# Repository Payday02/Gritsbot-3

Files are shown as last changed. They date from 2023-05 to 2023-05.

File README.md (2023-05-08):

# Gritsbot-3
This is an upgraded version of Gritsbot 2 from: https://github.gatech.edu/therobotcollective/gritsbot_2

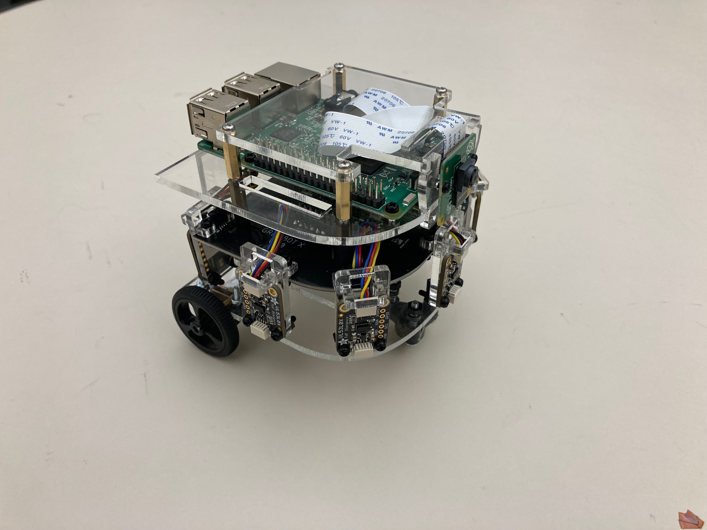
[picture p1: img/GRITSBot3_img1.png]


# Run The Teensy Demo

## 1 - Clone to your repo
```
git clone https://github.com/Payday02/Gritsbot-3.git
```

## 2 - Install Teensyduino / Arduino
For the Teensyduino, follow this link to install on Mac, Linux, and Windows: https://www.pjrc.com/teensy/td_download.html

## 3 - Locate Your Arduino Library
It should be under ```Arduino/Libraries```

## 4 - Copy and Paste the required libraries into the Arduino Library
Go back to the repo where you cloned Gritsbot-3.git
```
cp -a Gritsbot-3/firmware/library/. Arduino/Libraries
```
or

```
cd Gritsbot-3/firmware/library
```
and then copy everything in the library folder, then paste at Arduino/Libraries

## 5 - Run the Expo demo code
Go back to the repo where you cloned Gritsbot-3.git
```
cd Gritsbot-3/firmware/teensyCode/ExpoDemo
```

# Setup Process for the gritsbot\_3 (Need To Fix)(CheckPoint)

# 1 - Making the Base Image

This section details how to make the base image.  Relatively few changes are made to keep the image small.  Once the changes in this section have been made, copy the new image to an SD card and use that as the base image.

## 1 - Load the RPi image onto an SD card

Install latest Raspbian lite to an SD card.  Your .zip file may have a different name. Now, connect the SD card to your computer and unmount it with 
```
umount /dev/<your card>
``` 

You can see the card (probably) with 
```
lsblk
```

```
unzip -p 2018-10-09-raspbian-stretch-lite.zip | sudo dd status=progress of=/dev/sdX bs=4M conv=fsync 
```
 
Navigate to boot partition.  Place ssh, and wpa\_supplicant.conf files in boot partition.

```
cd <path_to>/boot
touch ssh 
touch wpa_supplicant.conf
```

Now, edit the wpa\_supplicant.conf file to something like the following.  Example WPA supplicant file:

```
ctrl_interface=DIR=/var/run/wpa_supplicant GROUP=netdev
update_config=1
country=US

network={
     ssid="Your network name/SSID"
     psk="Your WPA/WPA2 security key"
     key_mgmt=WPA-PSK
}
```

## 2 - Raspi Config

Boot the PI and ssh to it.  Then, launch

```
sudo raspi-config
```

Disable the **SSH console options, splash, and waiting for network on boot.** Enable **boot to the CLI**.  Remain SSHd to the RPi for the next steps.

## 3 - Disable Unused Services 

Add to /boot/config.txt the text

```
# Disable bluetooth
dtoverlay=pi3-disable-bt
```

# 2 - Automated Setup

This section assumes that you have built a base image as previously detailed.

## 1 - Automatic Installation

To install the firmware automatically, move the setup script to the directory /home/pi on the SD card.  Then, place the script setup\_service in the /etc/init.d directory.  When the pi starts, the items in this section will be automatically executed; then, the script deletes itself.  The log for the installation process can be viewed at /var/log/setup\_firmware.log

## 2 - Manual Installation

This section details the installation process for the firmware.  This process can be made automatic via the setup scripts.

### 1 Remove Unused Services

Remove plymouth with 

```
sudo apt-get purge --remove plymouth
```

Disable unused services with 

```
sudo systemctl disable triggerhappy.service
sudo systemctl disable hciuart.service
sudo systemctl disable keyboard-setup.service
sudo systemctl disable dphys-swapfile.service
```

### 2 - Install Docker

This section follows from the official (Docker)[https://docs.docker.com/install/linux/docker-ce/ubuntu/].  First, remove old versions of Docker.

```
sudo apt-get remove docker docker-engine docker.io
```

Next, install Docker using the convenience script.

```
curl -fsSL get.docker.com -o get-docker.sh && export VERSION=18.06 && sh get-docker.sh
```

Now tie Docker to the pi user so that we don't need sudo to use Docker.

```
sudo usermod -aG docker pi
```

### 3 - Clone Git Repos and install Deps

Install pip for python3

```
sudo apt-get install python3-pip
```

To clone the firmware, run
```
sudo apt-get install git
git clone https://github.com/robotarium/gritsbot_2
```

Also, install the MAC discovery repository
```
git clone https://github.com/robotarium/mac_discovery
```

as well as the python serial library used to communicate to the robot.

```
python3 -m pip install pyserial
```

### 4 - WiFi Power Management

Turn off power management by adding the line
```
/sbin/iw dev wlan0 set power_save off
```

in the file /etc/rc.local.  This line disables WiFi power management on boot.

### 5 - Start necessary containers

From wherever the git repository is cloned, run 
```
cd <path_to_gritsbot_2_repo>/docker
./docker_run.sh
./docker_watch.sh
```
which will permanently start a Docker container running the firmware and the watchtower container.  Watchtower watches containers and automatically updates them from Dockerhub.  This watchtower instance
checks and updates **all running containers**, so this instance will also update the MAC container as well.

Start MAC discovery as well with
```
cd <path_to_mac_discovery_repo>/docker
./docker_run.sh
```

# DEPRECATED - Setup Auto Deployment

Most of this info is from the (docker guide to registries)[https://docs.docker.com/registry/deploying/].

Alternatively, you may set up automatic deployment so that each robot updates on its own.  In this case, navigate to the registry directory and 
start the registry for the container.  

Obtain the registry on the **HOST** computer by running 
```
docker run -d -p 5000:5000 --restart=always --name registry registry:2
```
which will pull and run the container.  To only pull,
```
docker pull registry:2
```
should work

Under whatever the registry's computer's IP is, allow this in the file located at 
```
/etc/docker/daemon.json
```
In particular, add the lines
```
{ "insecure-registries": ["<ip_of_registry_computer>:5000"] }
```
Put in the IP right away.  **Errors in this script will kill the Docker service, so be careful!**

For example,
```
{ "insecure-registries": ["192.168.1.8:5000"] }
```
These lines must be added on the **host machine** as well as **all the robots.**  After you've added these lines, restart the Docker service with 
```
sudo /etc/init.d/docker restart
```

Push the firmware to the registry with 
```
docker tag robotarium:firmware <ip_of_registry_computer>:5000/firmware
docker push 192.168.1.8:5000/firmware
```
which will push the firmware container to the registry under the name firmware and the (default) latest tag.

You can check the current images maintained by the registry by checking the catalog with the command
```
curl -X GET 192.168.1.8:5000/v2/_catalog
```

Now, on the robot, navigate to the docker/deploy directory and build the robotarium:updater container.  This container will automatically update 
and restart the firmware container by pulling from the designated registry.

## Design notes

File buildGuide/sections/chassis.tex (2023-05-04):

\section{Chassis Assembly}
\label{sec:chassis}

Now that the main PCB of the GRITSBot X is assembled, it needs a chassis to be placed in. This section will detail how to manufacture and assemble the main chassis of the GRITSBOT X. The files associated with the production are available and editable. The Github repository contains Solid Works part files (SLDPRT), Adobe Illustrator files (AI), and PDF files. The PDF files should be able to be used for direct laser cutting of the chassis. The AI files may be used to edit the position of the cuts and duplicate the cuts for more to be produced at once. The SLDPRT files are what may be edited to change the chassis. Feel free to make whatever changes you would like to the design of the robot. This guide will assume that the construction is being done on the files provided.

\subsection{Laser Cutting the Chassis}
\label{sec:laserCut}

The chassis of the GRITSBot X are cut from $1/8$ inch thick and $1/16$ inch thick acrylic. The final cut pieces can be seen in \cref{fig:acrylicChassisCuts}. The files, \texttt{$GRITSBotX\_1\_8.ai$} and \texttt{$GRITSBotX\_1\_16.ai$} are files ready to produce the chassis through a 3D printer. The \texttt{$GRITSBotX\_1\_8$} is meant to create the $1/8$ inch thick acrylic parts and the \texttt{$GRITSBotX\_1\_16$} is meant to create the $1/16$ inch thick acrylic parts. {\color{red}Note}, these are sized for a $36 \times 24$ inch printer and in some cases the document side must be changed. Other alterations may have to be made for the specific laser cutter you are working on to cut and etch the right places in the file.

 %Laser Cut Pieces Picture
\begin{figure}[h!]
\centering
\subfloat[\label{fig:acrylic8}  $1/8$ inch thick acrylic chassis parts.]{}
\hfill
\subfloat[\label{fig:acrylic16} $1/16$ inch thick acrylic chassis parts.]{}\\
\caption{The $1/8$ (a) and $1/16$ (b) inch thick, custom cut acrylic chassis parts for the GRITSBot X.}
\label{fig:acrylicChassisCuts}
\end{figure}
%End Laser Cut Pieces Picture

Now that the acrylic chassis is cut for the GRITSBot X, the final assembly can begin!

\subsection{Assembling the Base}
\label{sec:base}

\subsubsection{Assembly Steps}
\begin{enumerate}
\item Gather the required materials(\cref{sec:baseMaterials}).
\item Assemble the motors and wheels (\cref{sec:motorAssembly}).
\item Put together the Tamiya caster wheel (\cref{sec:casterAssembly}).
\item Attach the motors and caster to the base plate(\cref{sec:baseAssembly}).
\end{enumerate}

\subsubsection{Required Materials}
\label{sec:baseMaterials}

As with the other sections, the first step is to gather the required materials. These are pictured in \cref{fig:baseMaterials} and listed in \cref{tab:baseMaterials}.

  %Begin Base Part Table
 \begin{table}[h!]
 \centering
\begin{tabular}{lc}
\rowcolor[HTML]{C0C0C0} 
\textbf{Part}  & \textbf{Number Required} 		\\
Acrylic Base Plate			&  1	\\
\rowcolor[HTML]{C0C0C0} 
Wheel               				& 2	\\
Micro-Metal Gear Motor	& 2	\\
\rowcolor[HTML]{C0C0C0} 
Motor Bracket Assembly	& 2   \\
Tamiya Caster Assembly	& 1	\\
\rowcolor[HTML]{C0C0C0} 
Compression Spring		& 3   \\
M3-20 Screw				& 3	\\
\rowcolor[HTML]{C0C0C0} 
M3 Locknut				& 3  
\end{tabular}
\caption{The parts required to assemble the base of the GRITSBot X. \label{tab:baseMaterials}}
\end{table}
 %End Base Part Table
 
 %Base Materials Picture
\begin{figure}[h!]
\centering

\caption{The materials needed to construct the base of the GRITSBot X.}
\label{fig:baseMaterials}
\end{figure}
%End Base Materials Picture

The acrylic base plate should have been laser cut in the previous step. The base plate can be recognized by the three screw holes in a triangular formation in the middle of the curved side of the chassis. This serves as the foundation of the GRITSBot X. The two wheels should come in one package from Pololu with the rubber tires separate from the plastic rims. The micro-metal gear motors from DFRobot come individually with corresponding jumper wires (not pictured here). Do not discard those, they will be used later.  The motor bracket assembly from Pololu should come as a pair with the nuts and screws pictured.  If the screws and nuts are lost they can easily be replaced, they are $\#2-56x7/16''$ screws with $\#2-56$ nuts. The Tamiya caster assembly come in packs of two. You only need one of the two and can keep the other for spare parts or keep this in mind when mass producing. The compression springs are meant as a pseudo suspension on the front caster to alleviate rattling and noise while the M3-20 screw and locknut keep the caster firmly attached to the base.

\subsubsection{Motor and Wheel Assembly}
\label{sec:motorAssembly}

The motor and wheel assembly is fairly straight forward but for consistency between robots details and tips are provided in this section. First, place the tires around the plastic rims. The tires are pretty elastic and can be stretched rather far. The tires on the rims should look like \cref{fig:tires} when finished.

%Tires Picture
\begin{figure}[h!]
\centering

\caption{GRITSBot X wheels fully assembled.}
\label{fig:tires}
\end{figure}
%End Tires Picture

These assembled wheels attach to the motors through a D-shaft. It is important to note the wheels have a flat side and side that sticks out. When pressing the wheel onto the D-shaft of the motor, make sure the flat side of the wheel is facing away from the motor. An easy way to attach the wheel to the D-shaft is to press the motor onto a flat surface through the wheel as pictured in \cref{fig:motorAssembly}. If you assemble this way, {\color{red}{be careful}} the encoder PCB is fragile and the magnetic disc can easily be moved. You are most likely to bend or break off the hall effect sensors (black rectangles sticking out of the PCB), so be careful where you place your hands/fingers when doing this.

%Motor Assembly Picture
\begin{figure}[h!]
\centering
\subfloat[\label{fig:pressMotor}  Pressing the motor D-shaft into the wheel.]{}
\hfill
\subfloat[\label{fig:motorSide} Side view of the motor and wheel assembly.]{}\\
\caption{The motor and wheel assembly pressure fit together.}
\label{fig:motorAssembly}
\end{figure}
%End Motor Assembly Picture

\subsubsection{Tamiya Caster Ball Assembly}
\label{sec:casterAssembly}

Since we are dealing with an \emph{differential drive} platform we need an additional, holonomic point of contact to passively stabilize the system. The GRITSBot X uses a Tamiya caster ball assembly with springs that provide a pseudo-suspension for this point of contact. Assembly instructions come with the Tamiya pack but an altered set of instructions will be provided here.

%Caster Parts Picture
\begin{figure}[h!]
\centering

\caption{The parts required to construct the caster ball assembly.}
\label{fig:casterParts}
\end{figure}
%End Caster Parts Picture

First, only the parts pictured in \cref{fig:casterParts} are needed. The springs, M3-20 screws, and M3 lock-nuts pictured at the bottom of the figure are not included in the kit. \cref{fig:casterAssembly} shows a picture representation of the assembly steps. A written explanation follows.

%Caster Assembly Picture
\begin{figure}[h!]
\centering
\subfloat[\label{fig:caster1} The caster holder with metal ball and cylindrical bearings inside.]{}
\hfill
\subfloat[\label{fig:caster2} Caster ball assembly with top plate properly inserted.]{}\\
\subfloat[\label{fig:caster3} Caster assembly with screws, springs, and plastic rings inserted.]{}
\hfill
\subfloat[\label{fig:casterFinished} The finished caster assembly attached to the bottom acrylic plate of the GRITSBot X.]{}\\
\caption{Process to put together the caster assembly.}
\label{fig:casterAssembly}
\end{figure}
%End Caster Assembly Picture

First, place the metal ball into the plastic caster shell. Place the three metal cylinders on top of the caster ball such that they fall into the rectangular slots in the plastic as seen in \cref{fig:caster1}. Cover this assembly with the second plastic piece provided by the caster kit. The cover should be placed so the triangle of the cover fits in the cutout of the caster ball holder as seen in \cref{fig:caster2}. There should be no gap between the cover and the caster container. Now that the caster is together, place the three M3 screws through the assembly such that the head of the screw is on the caster ball holder side of the assembly. Place the three springs around the screws. Put the three plastic rings over the springs. The screws with spring and plastic ring assembly should look like \cref{fig:caster3}. Push the screws through the holes of the acrylic base and lock them in place by threading them through the lock nuts. Make sure the screw is deep enough into the lock nut that the assembly will not come apart but not so tight that the spring is extremely compressed. This will be adjusted once the wheels are on to level the base.

If done correctly, the assembly should look like \cref{fig:casterFinished}. Test to make sure the caster is free moving by running your hand along the ball. It should move freely. If it doesn't, it's possible one of the metal cylinders came loose during assembly and is restricting the motion. If this is the case, the caster must be reassembled.

\subsubsection{Attaching the Motors and Caster to the Base Plate}
\label{sec:baseAssembly}

Finally, attach the motors to the base of the chassis. This is done by placing the motor bracket over the exposed gear box of the micro-metal gear motor as seen in \cref{fig:bracketMotor}. Note the plastic motor bracket has a rounded and rectangular surface as seen in \cref{fig:bracketDifference}. 

%Motor Bracket Picture
\begin{figure}[h!]
\centering
\subfloat[\label{fig:bracketDifference}  The rectangular opening (left) and curved opening (right) of the motor mounting brackets.]{}
\hfill
\subfloat[\label{fig:bracketMotor} Brackets properly attached to the micro metal gear motors.]{}\\
\caption{Attaching the brackets to the micro-metal gear motors properly.}
\label{fig:properMotorBracket}
\end{figure}
%End Motor Bracket Picture

Make sure the rounded surface rests on the hull of the motor and the rectangular surface rests on the gear box. This motor bracket should be put onto the motor such that the open side is on the same side as the motor connections for the encoder. Place the nut into the hexogonal space on the bracket and thread the screw through the acrylic into the motor bracket. Tighten the caster nuts as appropriate to make the chassis base as level as possible. The final assembly should look like \cref{fig:finalBase}.

%Finished Base Picture
\begin{figure}[h!]
\centering

\caption{The chassis base of the GRITSBot X.}
\label{fig:finalBase}
\end{figure}
%End Finished Base Picture

\subsection{Putting Together the Battery Bracket}
\label{sec:BB}

\subsubsection{Assembly Steps}
\label{sec:BBSteps}

\begin{enumerate}
\item Gather the required materials (\cref{sec:BBParts}).
\item Snap together the acrylic battery box (\cref{sec:BBBox}).
\item Attach the spacers for mounting the battery box and PCB (\cref{sec:BBSpacers}).
\end{enumerate}

\subsubsection{Required Materials}
\label{sec:BBParts}

The battery box assembly is fairly straight forward. The battery box housing is a pressure fit box created by the four $1/16$ inch acrylic parts cut earlier and pictured in the top of \cref{fig:acrylic16}. The housing is then supported and attached to the robot by threaded hexagonal spacers. The full list of materials needed is shown in \cref{tab:BBParts}.

%Begin Battery Box Part Table
 \begin{table}[h!]
 \centering
\begin{tabular}{p{3in}c}
\rowcolor[HTML]{C0C0C0} 
\textbf{Part}  & \textbf{Number Required} 		\\
Acrylic Battery Bracket Top/Bottom		& 2	\\
\rowcolor[HTML]{C0C0C0} 
Acrylic Battery Bracket Side				& 2	\\
4-40, $5/16$ inch Female to Female Hexagonal Standoff	& 4	\\
\rowcolor[HTML]{C0C0C0} 
4-40, $5/16$ inch Male to Female Hexagonal Standoff	& 4  \\
4-40, $3/16$ inch Nylon Male to Female Hexagonal Standoff	& 4
\end{tabular}
\caption{The parts required to assemble the battery bracket of the GRITSBot X. \label{tab:BBParts}}
\end{table}
 %End Battery Box Part Table

\subsubsection{Snapping Together the Battery Box}
\label{sec:BBBox}

The battery box is assembled through pressure/press fitting tabs together to form a box. It should be noted this is a fairly delicate ($1/16$ inch acrylic is brittle and fragile) and precise process. If your laser cutter cuts wider or narrower paths than the one at Georgia Tech, the tab widths may have to be altered.

To begin, press fit two of the side pieces into a top/bottom piece as seen in \cref{fig:box1}. Note, if this seems to tight to do or the tabs don't hold together, the tab widths needs to be adjusted for your laser cutter. The best process to do this is to press in the center tab followed by the outside tabs. Try not to snap the acrylic during this.

%Battery Bracket Assembly Picture
\begin{figure}[h!]
\centering
\subfloat[\label{fig:box1} Battery bracket sides pressure fit into a top/bottom.]{}
\hfill
\subfloat[\label{fig:box2} Final battery bracket assembly.]{}\\
\caption{Pressure/Press fitting together the battery bracket for the GRTISBot X.}
\label{fig:batteryBox}
\end{figure}
%End Battery Bracket Assembly Picture

Finally, press fit the top piece into the assembly just snapped together as seen in \cref{fig:box2}. It is much easier to press fit one side at a time. The joints should rotate fairly easily so you can press one at a time. pressing the assembly into the side of a table or book spine helps tremendously.

\subsubsection{Attaching the Mounting Spacers}
\label{sec:BBSpacers}

Finally, attach the hexagonal spacers to the battery box so it may be mounted to the base of the GRITSBot X and support the PCB in the next steps. Place the four $5/16$ female to female hexagonal spacers between the battery bracket (this can be done one at a time. Screw the four $5/16$ male to female hexagonal spacers into one side of the female to female spacers between the battery bracket. On the other side screw the four $3/16$ male to female nylon hexagonal spacers into the battery bracket. The resulting assembly should look like \cref{fig:finalBatteryBracket}.

 %Battery Bracket Finished Picture
\begin{figure}[h!]
\centering

\caption{The finished battery bracket assembly with hexagonal stand off supports attached.}
\label{fig:finalBatteryBracket}
\end{figure}
%End Battery Bracket Finished Picture

\subsection{Attaching the Cassis Base, Battery Bracket, and PCB}
\label{sec:finishBase}

\subsubsection{Assembly Steps}
\label{sec:finishBaseSteps}

\begin{enumerate}
\item Gather the required materials (\cref{sec:finishBaseMaterials}).
\item Attach the battery box to the chassis base (\cref{sec:BBtoCB}).
\item Attach the PCB to the chassis base assembly (\cref{sec:attachPCB}).
\end{enumerate}

\subsubsection{Required Materials}
\label{sec:finishBaseMaterials}

Connecting the chassis base, battery bracket, and PCB is, again, straightforward and just requires screwing the parts created previously together. The full list of materials needed are in \cref{tab:finishBaseParts}.

%Begin Chassis Base Part Table
 \begin{table}[h!]
 \centering
\begin{tabular}{p{3in}c}
\rowcolor[HTML]{C0C0C0} 
\textbf{Part}  & \textbf{Number Required} 		\\
Assembled Chassis Base from \cref{sec:base}		& 1	\\
\rowcolor[HTML]{C0C0C0} 
Assembled Battery Bracket from \cref{sec:BB}				& 1	\\
Finished PCB from \cref{sec:pcb}	& 1	\\
\rowcolor[HTML]{C0C0C0} 
4-40, $1/4$ inch Screw	& 4  \\
4-40, $3/4$ inch Nylon Male to Female Hexagonal Standoff	& 4\\
\rowcolor[HTML]{C0C0C0} 
3.7V 2500mAh Adafruit Li-Po Battery	& 1
\end{tabular}
\caption{The parts required to combine the chassis base, battery bracket, and PCB of the GRITSBot X. \label{tab:finishBaseParts}}
\end{table}
 %End Chassis Base Part Table

\subsubsection{Attaching the Battery Box to the Chassis Base}
\label{sec:BBtoCB}

The battery bracket assembly (\cref{fig:finalBatteryBracket}, assembly instructions in \cref{sec:BB}) attaches directly to the chassis base (\cref{fig:finalBase}, assembly instructions in \cref{sec:base}) Screw the four 4-40, $1/4$ inch screws,  through the bottom of the four remaining holes in the acrylic base plate into the four 4-40, $5/16$ inch hexagonal standoffs. If done properly, the battery bracket, chassis base assembly should look like \cref{fig:BBtoBC}.

 %Battery Bracket Chassis Finished Picture
\begin{figure}[h!]
\centering

\caption{The base chassis with batter bracket attached.}
\label{fig:BBtoBC}
\end{figure}
%End Battery Bracket Chassis Finished Picture

\subsubsection{Attaching the PCB}
\label{sec:attachPCB}

Attaching the PCB is a little trickier simply because the motor leads danging from the PCB must be attached to the motor and the battery lead must be run in a somewhat smart way. The PCB aligns with the chassis shape, the round part of the board should line up with the round part of the chassis when attached. The top of the PCB has the Teensy micro-controller on it. After orienting it correctly, the four holes on the board should line up with the four 4-40, $3/16$ inch nylon hexagonal stand offs. Before securing the PCB into place, run the motor leads around the side of the battery box, underneath it, along the base acrylic, and out between the motor connections. The left lead from the PCB should insert into the left motor and right lead from the PCB should insert into the right motor. {\color{red}{Note}}, there is a tab on the connection so it should only insert one way but can be forced in the wrong way which will break the robot if powered on this way!

To clean up the excess wire push it back underneath the battery bracket such that there is enough room to insert the 3.7V Li-Po battery into the battery box. Insert the battery such that the lead comes out the back (flat side of the chassis) of the robot. Run the lead under the battery bracket (above the base acrylic) and out the left side of the robot to the battery connector (black plastic connector towards the back left corner of the PCB). {\color{red}{Note}}, make sure the lead of the battery is bent away from the wheel so it does not get caught and stall the robot or wear away the insulation. The wiring should look like \cref{backAttachPCB} when finished.

If done correctly the robot with the PCB in place should look like \cref{fig:attachPCB}.

%Battery Bracket Assembly Picture
\begin{figure}[h!]
\centering
\subfloat[\label{fig:topAttachPCB} Top view of the GRITSBot X with PCB attached to the chassis base.]{}
\hfill
\subfloat[\label{fig:backAttachPCB} Back view of the GRITSBot X with PCB attached to the chassis base.]{}\\
\caption{The GRITSBot X without top assembly.}
\label{fig:attachPCB}
\end{figure}
%End Battery Bracket Assembly Picture

\subsection{Assembling and Attaching the Chassis Cover}
\label{sec:topPlate}

\subsubsection{Assembly Steps}
\label{sec:topPlateSteps}

\begin{enumerate}
\item Gather the required materials (\cref{sec:topPlateMaterials}).
\item Attach the Raspberry Pi to the Zero4U through the top acrylic plate (\cref{sec:attachZero4U}).
\item Attach the chassis top assembly to the base assembly (\cref{sec:attachChassisTop}).
\end{enumerate}

\subsubsection{Required Materials}
\label{sec:topPlateMaterials}

The chassis is nearly assembled and thus, there are not many materials needed for this step. The few needed are  listed in \cref{tab:topPlateMaterials}.

%Top Chassis Materials Picture
\begin{figure}[h!]
\centering

\caption{The parts required to assemble and attach the chassis cover of the GRITSBot X.}
\label{fig:topPlateMaterials}
\end{figure}
%End Top Chassis Materials  Picture

 %Begin Chassis Top Part Table
 \begin{table}[h!]
 \centering
\begin{tabular}{p{3in}c}
\rowcolor[HTML]{C0C0C0} 
\textbf{Part}  & \textbf{Number Required} 		\\
Assembled Chassis Base from \cref{sec:finishBase}		& 1	\\
\rowcolor[HTML]{C0C0C0} 
Acrylic Top Plate			& 1	\\
Raspberry Pi Zero with Soldered Leads from \cref{sec:raspberryPiLeads}	& 1	\\
\rowcolor[HTML]{C0C0C0} 
Zero4U 4-Port USB Hub	 Kit	& 1 \\
Tracking Hat				& 1 \\
\rowcolor[HTML]{C0C0C0} 
4-40, $1/2$ inch Screw	& 4  \\
4-40 Locknut	& 4\\
\rowcolor[HTML]{C0C0C0} 
4-40, $1/4$ inch Screw	& 4  \\
4-40, $5/8$ inch Male to Female Hexagonal Standoff	& 4\\
\end{tabular}
\caption{The parts required to assemble and attach the chassis cover of the GRITSBot X. \label{tab:topPlateMaterials}}
\end{table}
 %End Chassis Top Part Table

\subsubsection{Attaching the Peripheral Circuit Boards to the Top Chassis}
\label{sec:attachZero4U}

pictured in \cref{fig:topPlateMaterials} and

The first step in this assembly is to attach the Raspberry Pi Zero W \cite{raspberryPiZeroW} to the Zero4U 4-port USB hub \cite{zero4u}. This allows the Raspberry Pi Zero W to connect to the Teensy using a readily available on-the-go (OTG) USB cable as well as extend its wireless communication capabilities with a USB Wi-Fi antenna or other peripherals with limited current draw.

%Top Chassis Materials Picture
\begin{figure}[h!]
\centering

\caption{The parts required to assemble and attach the chassis cover of the GRITSBot X.}
\label{fig:topPlateMaterials}
\end{figure}
%End Top Chassis Materials  Picture

The parts needed for this are pictured in \cref{fig:topPlateMaterials}. Insert the four 4-40, $1/2$ inch screws through the Zero4U such that the head of the screw is on the same side as the USB ports. Slide the four plastic spacers provided with  the Zero4U kit onto the screws. Slide the green ferrite ring around the two pins that are parallel to the long edge of the board \cite{zero4uRing}. Place the screws through the four wider holes in the acrylic top plate. The Zero4U board should be on the top of the acrylic plate (the side with the etching or the side with the off center rectangular cut on the right with the curved surface being the front). Finally, place the Raspberry Pi Zero W on the other side and thread the screws through the corresponding four screw holes. The metal pins from the Zero4U should align with the exposed pads on the opposite side of the USB ports on the Raspberry Pi. If done correctly, the assembly should look like \cref{fig:topChassisAssembled}.

%Chassis Top Assembly Picture
\begin{figure}[h!]
\centering
\subfloat[\label{fig:topAttachPCB} Top view of the chassis cover.]{}
\hfill
\subfloat[\label{fig:backAttachPCB} Bottom view of the chassis cover.]{}\\
\caption{The GRITSBot X chassis cover.}
\label{fig:topChassisAssembled}
\end{figure}
%End Chassis Top Assembly Picture

\subsubsection{Attaching the Chassis Cover to the Base Chassis}
\label{sec:attachChassisTop}

The final step is to attach this chassis cover to the base built in \cref{sec:finishBase}. The parts needed for this are pictured in \cref{fig:finalChassisMaterials}.

%Top Chassis Materials Picture
\begin{figure}[h!]
\centering

\caption{The parts required to the chassis cover to the base of the GRITSBot X.}
\label{fig:finalChassisMaterials}
\end{figure}
%End Top Chassis Materials  Picture

First, insert the power jumper from the Raspberry Pi Zero into the JST connector in the lower right of main PCB of the GRITSBot X. It should only fit one way but can be forced in the wrong way. {\color{red}{Note}}, if this wire is plugged in the wrong way with the robot powered on, the Raspberry Pi Zero W will probably be destroyed and other components on the PCB can also be destroyed. Make sure the plastic tab on the end of the jumper cable aligns with the hole on the PCB. \cref{fig:pluggedPi} pictures the jumper plugged into the PCB correctly.

%Plugged in Pi Picture
\begin{figure}[h!]
\centering

\caption{The Raspberry Pi Zero W correctly plugged into the main PCB of the GRITSBot X.}
\label{fig:pluggedPi}
\end{figure}
%End Plugged in Pi  Picture

After plugging in the Raspberry Pi Zero W place the top acrylic onto the standoffs and secure it with the four 4-40, $5/8$ inch male to female hexagonal standoff. The outer shape of the top plate should align with the bottom plate and the Raspberry Pi Zero W should be on the interior of the robot. If done correctly, the robot without its finishing touches should look like \cref{fig:nearFinalChassis}.

%Final Chassis Picture
\begin{figure}[h!]
\centering

\caption{The chassis base with chassis cover attached.}
\label{fig:nearFinalChassis}
\end{figure}
%End Plugged in Pi  Picture

\subsection{The Final Touches}
\label{sec:finalTouch}

\subsubsection{Assembly Steps}
\label{sec:finalAssembly}

\begin{enumerate}
\item Gathe the required materials (\cref{sec:finalMaterials}).
\item Plug in the periferal electronics (\cref{sec:plugIn}).
\item Attach the charging plate (\cref{sec:chargingPlate}).
\item CELEBRATE FINISHING! (\cref{sec:CELEBRATE}).
\end{enumerate}

\subsubsection{Required Materials}
\label{sec:finalMaterials}

The final step is to connect the Teensy and Raspbeery Pi Zero W so they can communicate over serail, add a Wi-Fi antenna to boost signal reception, and attach the charging plate. A picture of the required materials is in \cref{fig:finalMaterials} with a table listing them in \cref{tab:finalMaterials}.

%Final Matrials Picture
\begin{figure}[h!]
\centering

\caption{The materials needed to finish the assembly of the GRITSBot X.}
\label{fig:finalMaterials}
\end{figure}
%End Materials  Picture

 %Begin Final Part Table
 \begin{table}[h!]
 \centering
\begin{tabular}{p{3in}c}
\rowcolor[HTML]{C0C0C0} 
\textbf{Part}  & \textbf{Number Required} 		\\
Assembled GRITSBot X from \cref{sec:topPlate}		& 1	\\
\rowcolor[HTML]{C0C0C0} 
Acrylic Charging Back Plate			& 1	\\
Acrylic Charging Front Plate		& 1	\\
\rowcolor[HTML]{C0C0C0} 
Digiyes Qi Charging Reciever	& 1 \\
Short Micro USB Noodle Cable				& 1 \\
\rowcolor[HTML]{C0C0C0} 
LB-Link Wireless USB Adapter	& 1  \\
\end{tabular}
\caption{The parts required to finish the assmbly of the GRITSBot X. \label{tab:finalMaterials}}
\end{table}
 %End Final Part Table

\subsubsection{Attaching Periferal Electronics}
\label{sec:plugIn}

First connect the short micro USB noodle cable between the middle usb port on top of the robot and the micro USB port on the Teensy board inside the robot (\cref{fig:microUSB}). Next insert the micro usb connector of the Digiyes Qi charging receiver into the connector next to the battery connection on the PCB (\cref{fig:qiCharger}). You robot should resemble that in \cref{fig:attachedElectronics} at this point. You may now insert the LB-Link wireless USB adapter into one of the slots next to the micro USB noodle cable.

%Electronics Plugged in Picture
\begin{figure}[h!]
\centering
\subfloat[\label{fig:microUSB} The micro USB cable connecting the Rapsberry Pi (through the Zero4U) and Teensy.]{}
\hfill
\subfloat[\label{fig:qiCharger} The Digiyes Qi charging reciever plugged in properly.]{}\\
\caption{The GRITSBot X with electronics properly attached.}
\label{fig:attachedElectronics}
\end{figure}
%End Electronics Plugged in Picture

\subsubsection{Attaching the Wireless Charger}
\label{sec:chargingPlate}

To finish the robot, the Qi wireless charger needs to be secured. Insert the acrylic back plate (the one without etching) of the charger into the slots in the top and bottom acylic plate of the chassis. It should slide in freely. Next, put the charging coil over this plate and fold the excess between the IR sensor and charging plate. It is best to route the connecting cable over the top of the PCB. {\color{red}{Do not}}, cover the IR sensor with the excess of the charging pad. Finally snap the front plate into the same four slots of the bottom and top of the chassis. Make sure the etching is facing out so the Robotarium logo is not reflected! If done correctly, the back of the robot should look like \cref{fig:finishedBack}.

%Final Back Picture
\begin{figure}[h!]
\centering

\caption{The charging plate of the GRITSBot X properly attached.}
\label{fig:finishedBack}
\end{figure}
%End Back  Picture

\subsubsection{CELEBRATE!}
\label{sec:CELEBRATE}

Congratulations! The GRITSBot X is completely assembled. You may move onto the next guide to get the software up and running and then begin programming your robot to do super cool tasks!

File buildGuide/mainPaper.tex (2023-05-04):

\documentclass[11pt]{article} % use larger type; default would be 10pt

% misc packages
\usepackage{subfiles}
\usepackage{csquotes}
\usepackage{graphicx}
\usepackage{subfig}
%
\usepackage[numbers]{natbib}

%% Setup for links, auto referencing, and indexing
\input{_preamble_hyperref}

%Fake Section to Suppress Section Title if wanted
\newcommand{\fakesection}[1]{%
  \par\refstepcounter{section}% Increase section counter
  \sectionmark{#1}% Add section mark (header)
  \addcontentsline{toc}{section}{\protect\numberline{\thesection}#1}% Add section to ToC
  % Add more content here, if needed.
}

% The paper headers
\usepackage{fancyhdr}
\pagestyle{fancy}
\fancyhf{}
\rhead{\thepage}
\lhead{GRITSBot X Construction Guide}

\begin{document}
%

\title{GRITSBot X \\ \Large{Construction Guide}}

\author{Sean Wilson\\Sean.T.Wilson@gatech.edu}% <-this % stops a space

% make the title area
\maketitle
\thispagestyle{empty} %Get rid of number on first page

\tableofcontents
\clearpage

{\let\thefootnote\relax\footnote{The work reported here was sponsored by the US National Science Foundation through grant numbers 1531195 and 1544332, and by the Office for Naval Research through grant number N00014-17-1-2323.}}

\subfile{sections/introduction}
\subfile{sections/pcb}
\subfile{sections/chassis}

%%%%%%%%%%%%%%%%%%%%%%%%%%%%%%%%%%%%%%%%%%%%%%%%%%%%%%%%%%%%%%
%Bibliography Stuff
\clearpage
\bibliographystyle{unsrtnat}
\bibliography{mainPaper.bib}

\end{document}

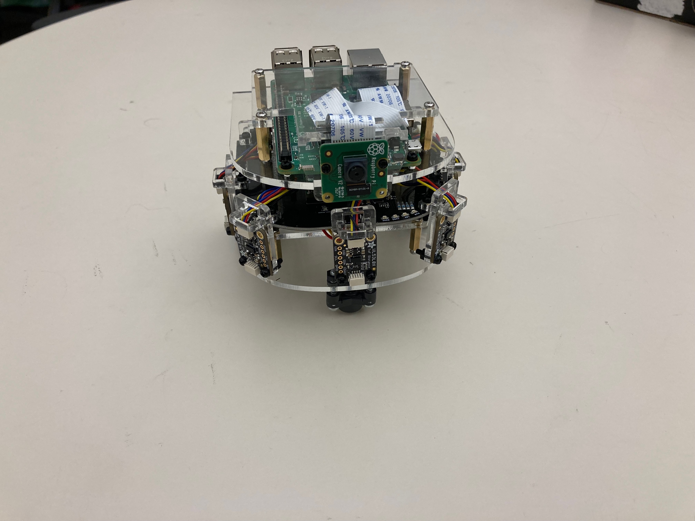
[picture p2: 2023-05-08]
img/GRITSBot3_img4.png

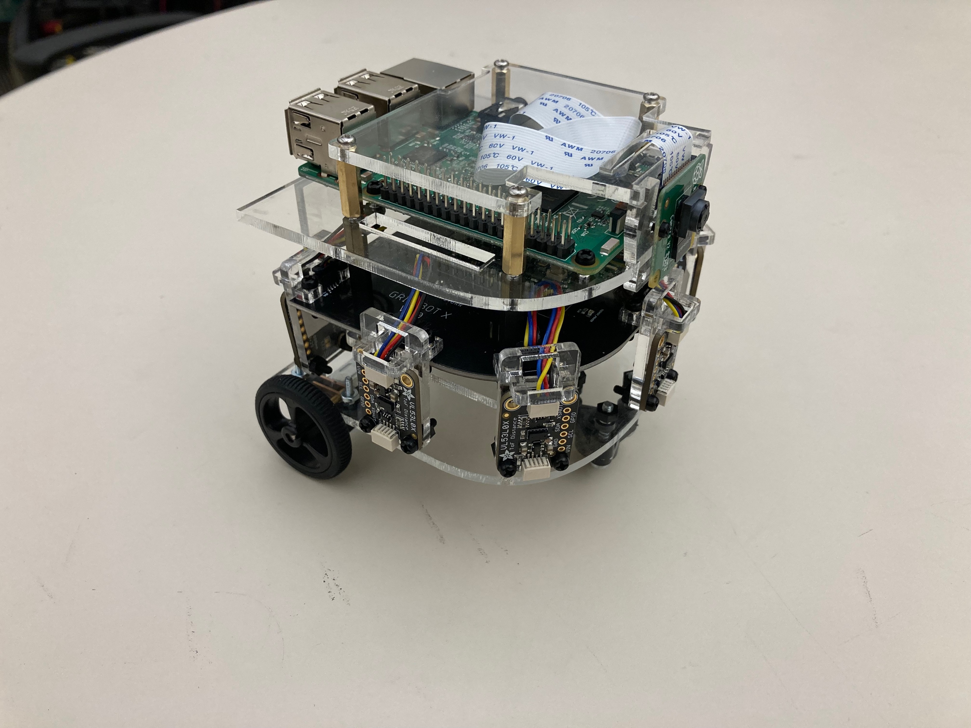
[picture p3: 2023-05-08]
img/GRITSBot3_img5.png

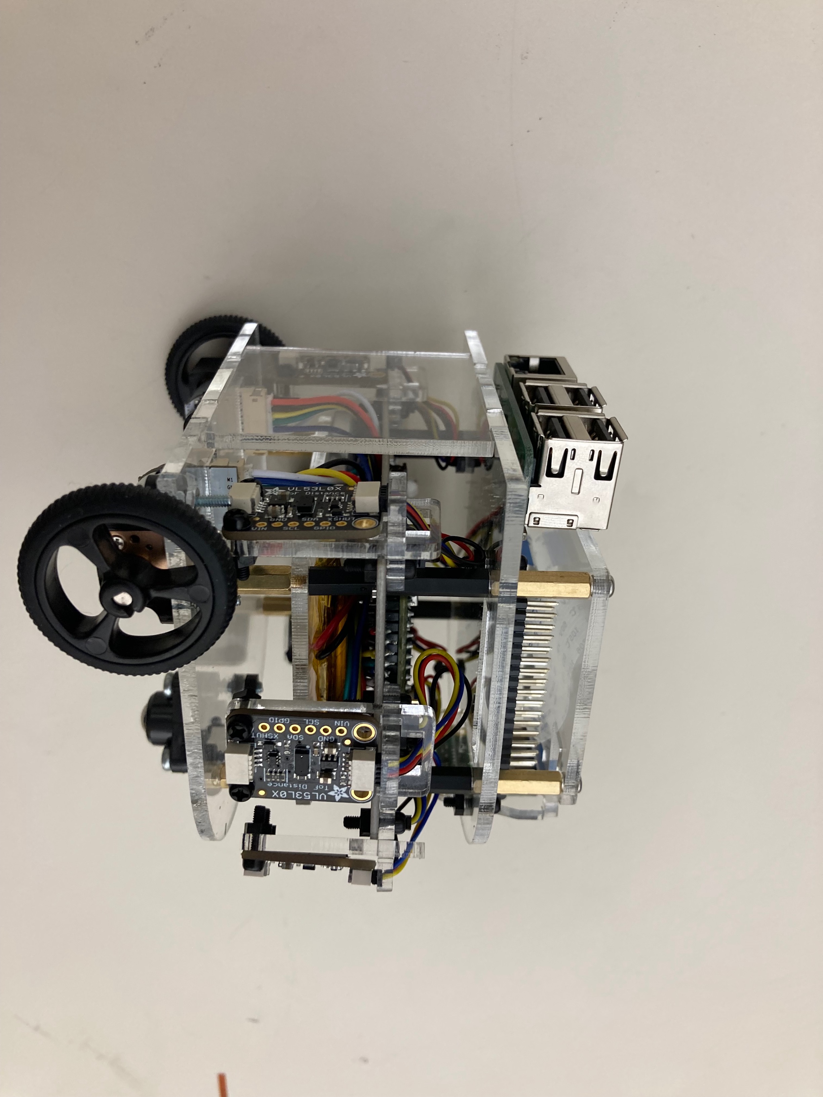
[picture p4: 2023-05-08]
img/GRITSBot3_img2.png

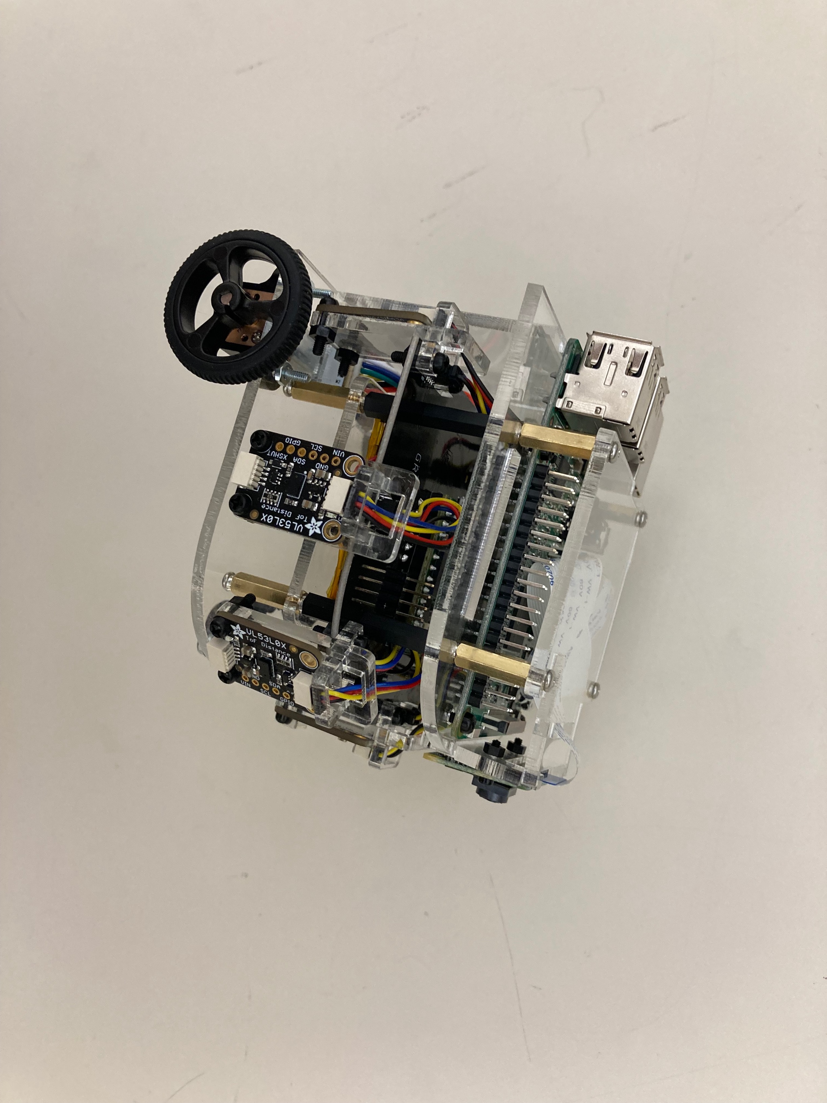
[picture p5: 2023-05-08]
img/GRITSBot3_img7.png

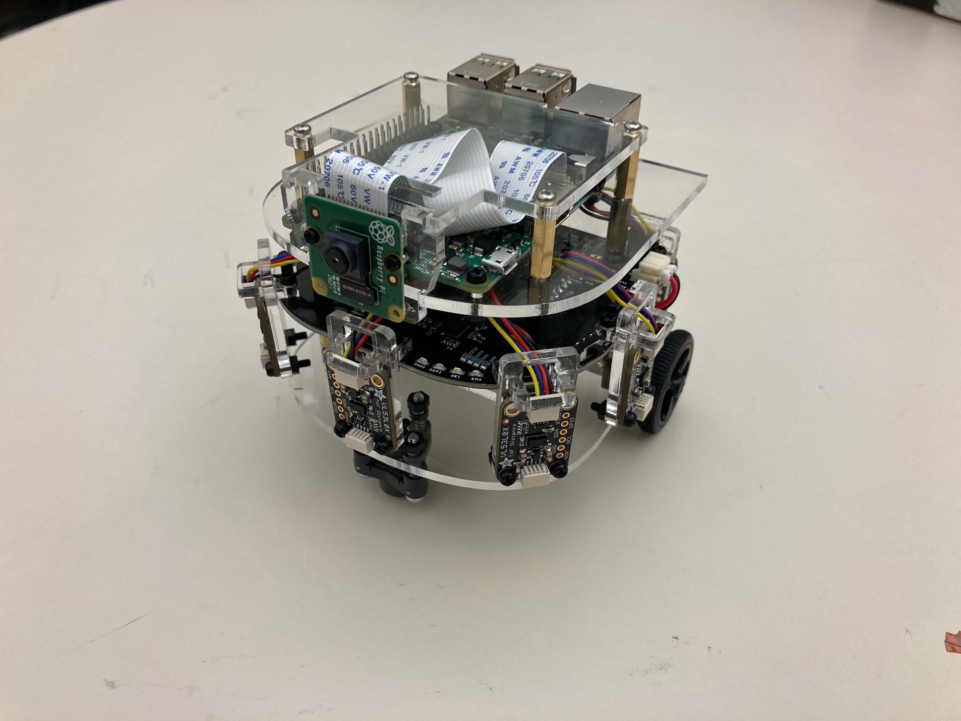
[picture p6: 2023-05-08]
img/GRITSBot3_img6.png

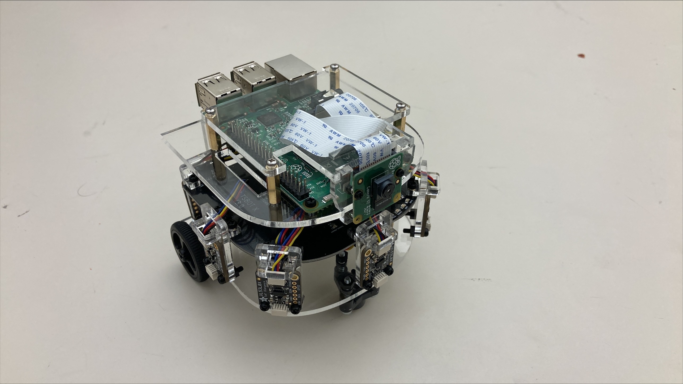
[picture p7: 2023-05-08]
img/GRITSBot3_img3.png

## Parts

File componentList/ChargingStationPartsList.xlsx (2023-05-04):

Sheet: Single Station
Item | Price Per Item | Number Needed | Total Price | Order Link | Description
1/2’’ 4-40 Screws | $1.75 | 0.04 | $0.07 | https://www.mcmaster.com/90272A110 | Attaching charging PCB to mounting.
3/4'' 4-40 Flathead Screws | $4.08 | 0.02 | $0.08 | https://www.mcmaster.com/90273A113 | Attaching mounting plate to charging plate.
3'' 4-40 Screws | $8.71 | 0.04 | $0.35 | https://www.mcmaster.com/90272A287 | Screw to attach charger to the wall.
4-40 Washer | $1.40 | 0.04 | $0.06 | https://www.mcmaster.com/92141A005 | Washer for mounting plate to charging plate connection.
3/16'' Aluminum F-F Threaded Hex Standoff | $0.46 | 4 | $1.84 | https://www.mcmaster.com/91780A523 | Spacer between acryllic mounting and PCB.
1/4'' Aluminum F-F Threaded Hex Standoff | $0.50 | 4 | $2.00 | https://www.mcmaster.com/91780A525 | Spacer between acryllic charging plate and mounting.
4-40 Nylon Lock Nut | $12.87 | 0.04 | $0.51 | https://www.mcmaster.com/94909A005 | Lock nuts to secure charging plate and rub against mounting wall.
4-40 Metal Lock Nut | $2.79 | 0.06 | $0.17 | https://www.mcmaster.com/90631A005 | Lock nuts to secure PCB and mouting plate.
24’’ x 36’’ - 1/8’’ Thick Clear Acrylic Sheet | $27.80 | 0.005882352941 | $0.16 | http://a.co/d/gHgLLsl | Acrylic sheet to laster cut for charging plate.
24’’ x 24’’ - 1/16’’ Thick Clear Acrylic Sheet | $19.99 | 0.05882352941 | $1.18 | http://a.co/d/isk6QyS | Acrylic sheet to be laser cut for and charging plate.
USB Cord | $4.99 | 1 | $4.99 | http://a.co/d/faIFx2a | USB cord to connect to power source.
Universal Qi Wireless Transmitter | $26.95 | 1 | $26.95 | https://www.adafruit.com/product/2162 | Qi wireless charger.
Total |  |  | $38.36

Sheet: Multiple Stations
Number of Stations Required | 36
Item | Price Per Item | Number Needed | Total Price | Order Link | Description | Order Location Color
1/2’’ 4-40 Screws | $1.75 | 2 | $3.50 | https://www.mcmaster.com/90272A110 | Attaching charging PCB to mounting.
3/4'' 4-40 Flathead Screws | $4.08 | 1 | $4.08 | https://www.mcmaster.com/90273A113 | Attaching mounting plate to charging plate.
3'' 4-40 Screws | $8.71 | 2 | $17.42 | https://www.mcmaster.com/90272A287 | Screw to attach charger to the wall.
4-40 Washer | $1.40 | 2 | $2.80 | https://www.mcmaster.com/92141A005 | Washer for mounting plate to charging plate connection.
3/16'' Aluminum F-F Threaded Hex Standoff | $0.46 | 144 | $66.24 | https://www.mcmaster.com/91780A523 | Spacer between acryllic mounting and PCB.
1/4'' Aluminum F-F Threaded Hex Standoff | $0.50 | 144 | $72.00 | https://www.mcmaster.com/91780A525 | Spacer between acryllic charging plate and mounting.
4-40 Nylon Lock Nut | $12.87 | 2 | $25.74 | https://www.mcmaster.com/94909A005 | Lock nuts to secure charging plate and rub against mounting wall.
4-40 Metal Lock Nut | $2.79 | 3 | $8.37 | https://www.mcmaster.com/90631A005 | Lock nuts to secure PCB and mouting plate.
24’’ x 36’’ - 1/8’’ Thick Clear Acrylic Sheet | $27.80 | 1 | $27.80 | http://a.co/d/gHgLLsl | Acrylic sheet to laster cut for charging plate.
24’’ x 24’’ - 1/16’’ Thick Clear Acrylic Sheet | $19.99 | 3 | $59.97 | http://a.co/d/isk6QyS | Acrylic sheet to be laser cut for and charging plate.
USB Cord | $4.99 | 36 | $179.64 | http://a.co/d/faIFx2a | USB cord to connect to power source.
Universal Qi Wireless Transmitter | $26.95 | 36 | $970.20 | https://www.adafruit.com/product/2162 | Qi wireless charger.
Total |  |  | $1437.76

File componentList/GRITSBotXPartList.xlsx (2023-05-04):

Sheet: Single GRITSBotX
Item | Price Per Item | Number Needed | Total Price | Order Link | Description
5/16’’Aluminum M-F Threaded Hex Standoff | $0.80 | 4 | $3.20 | https://www.mcmaster.com/93505A466 | Aluminum stand off for attaching bottom acrylic to battery holder acrylic
5/16’’ Aluminum F-F Threaded Hex Standoff | $0.52 | 4 | $2.08 | https://www.mcmaster.com/91780A527 | Aluminum stand off spacing the battery holder.
3/16’’ Nylon M-F Threaded Hex Standoff | $2.70 | 4 | $10.80 | https://www.mcmaster.com/92745A460 | Nylon stand off for attaching main PCB to battery holder.
3/4’’ Nylon M-F Threaded Hex Standoff | $2.97 | 4 | $11.88 | https://www.mcmaster.com/92745A380 | Nylon stand off for attaching main PCB to top acrylic.
1/4’’ 4-40 Screws | $1.46 | 0.08 | $0.12 | https://www.mcmaster.com/90272A106 | Attaching bottom acrylic to standoff. Screws come in 100 pack bags
1/2’’ 4-40 Screws | $1.75 | 0.04 | $0.07 | https://www.mcmaster.com/90272A110 | Attaching Raspberry Pi to top acrylic. Screws come in 100 pack bags
4-40 Metal Lock Nut | $2.79 | 0.04 | $0.17 | https://www.mcmaster.com/90631A005 | Lock nuts to secure Raspberry Pi and top mouting plate.
3/16’’ Aluminum F-F Threaded Hex Standoff | $0.46 | 4 | $1.84 | https://www.mcmaster.com/91780A523 | Aluminum stand off for attaching Raspberry Pi to top acrylic.
1/2’’ M3 Screws | $4.37 | 0.03 | $0.13 | https://www.mcmaster.com/92005A124 | Screws for attaching caster to chassis
M3 Nylon Lock Nuts | $3.45 | 0.03 | $0.10 | https://www.mcmaster.com/90576A102 | Lock nuts for attaching caster to chassis
24’’ x 36’’ - 1/8’’ Thick Clear Acrylic Sheet | $27.80 | 0.08333333333 | $2.32 | http://a.co/d/gHgLLsl | Acrylic sheet to laster cut for robot chassis.
24’’ x 24’’ - 1/16’’ Thick Clear Acrylic Sheet | $19.99 | 0.125 | $2.50 | http://a.co/d/isk6QyS | Acrylic sheet to be laser cut for battery holder and charging plate.
8’’ M-M Micro USB to Micro USB | $5.06 | 1 | $5.06 | http://a.co/d/02ey9tC | USB to connect the Raspberry Pi Zero to Teensy
DiGiYes Wireless Charging Receiver | $10.00 | 1 | $10.00 | http://a.co/d/eJUInFT | Wireless charging receiver (optional for non Robotarium use)
Lithium Ion Polymer Battery - 3.7v 2500mAh | $14.95 | 1 | $14.95 | https://www.adafruit.com/product/328 | Battery to power the robot.
Teensy 3.2 Microcontroller | $19.95 | 1 | $19.95 | https://www.adafruit.com/product/2756 | Low level micro-controller
Raspberry Pi Zero W Basic Pack | $24.50 | 1 | $24.50 | https://www.adafruit.com/product/3409 | High Level Processor
JST PH 2-Pin Cable - Female Connector 100mm | $0.75 | 1 | $0.75 | https://www.adafruit.com/product/261 | Power Cable Jumper for Raspberry Pi
Micro Metal Gear Motor with Encoder (100:1 gearing) | $11.50 | 2 | $23.00 | https://www.dfrobot.com/product-1433.html | Motors for the robot.
Pololu Micro Metal Gearmotor Bracket Pair – Black | $4.99 | 1 | $4.99 | https://www.pololu.com/product/989 | Mount for securing motors to acrylic chassis
Pololu Wheel 32×7mm Pair – Black | $4.98 | 1 | $4.98 | https://www.pololu.com/product/1087 | Wheels that attach to the motors.
Pololu Carrier with Sharp GP2Y0A60SZLF Analog Distance Sensor 10-150cm, 5V | $12.17 | 7 | $85.19 | https://www.pololu.com/product/2474 | IR Range Sensors
Tamiya Caster Ball | $5.95 | 0.5 | $2.98 | https://www.sparkfun.com/products/320 | Caster Ball to Balance Robot
SWITCH SLIDE SPST 500MA 125V | $1.30 | 1 | $1.30 | https://www.digikey.com/short/jfcbcq | Main Power Switch for Robot
CONN HEADER PH TOP 2POS 2MM | $0.17 | 1 | $0.17 | https://www.digikey.com/short/jfcjf3 | Power Jumper for Pi to Main Board
BERGSTIK HDR 14POS .100" DR SMT | $1.44 | 1 | $1.44 | https://www.digikey.com/short/jbdd3f | Header pins for underside of Teensy 3.2
Compression Spring | $2.00 | 3 | $6.00 | https://www.springsfast.com/part_detail_compression.php?part=C05-014-008 | Spring for pseudo suspension on the caster ball of the robot (avoids rattle)
Total |  |  | $234.46

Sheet: Multiple GRITSBotX
Number of Robots Required | 55
Item | Price Per Item | Number Needed | Total Price | Order Link | Description | Order Location Color
5/16’’Aluminum M-F Threaded Hex Standoff | $0.80 | 220 | $176.00 | https://www.mcmaster.com/93505A466 | Aluminum stand off for attaching bottom acrylic to battery holder acrylic
5/16’’ Aluminum F-F Threaded Hex Standoff | $0.52 | 220 | $114.40 | https://www.mcmaster.com/91780A527 | Aluminum stand off spacing the battery holder.
3/16’’ Nylon M-F Threaded Hex Standoff | $2.70 | 220 | $594.00 | https://www.mcmaster.com/92745A460 | Nylon stand off for attaching main PCB to battery holder.
3/4’’ Nylon M-F Threaded Hex Standoff | $2.97 | 220 | $653.40 | https://www.mcmaster.com/92745A380 | Nylon stand off for attaching main PCB to top acrylic.
1/4’’ 4-40 Screws | $1.46 | 5 | $7.30 | https://www.mcmaster.com/90272A106 | Attaching bottom acrylic to standoff. Screws come in 100 pack bags
1/2’’ 4-40 Screws | $1.75 | 3 | $5.25 | https://www.mcmaster.com/90272A110 | Attaching Raspberry Pi to top acrylic. Screws come in 100 pack bags
4-40 Metal Lock Nut | $2.79 | 3 | $8.37 | https://www.mcmaster.com/90631A005 | Lock nuts to secure Raspberry Pi and top mouting plate.
3/16’’ Aluminum F-F Threaded Hex Standoff | $0.46 | 220 | $101.20 | https://www.mcmaster.com/91780A523 | Aluminum stand off for attaching Raspberry Pi to top acrylic.
1/2’’ M3 Screws | $4.37 | 2 | $8.74 | https://www.mcmaster.com/92005A124 | Screws for attaching caster to chassis
M3 Nylon Lock Nuts | $3.45 | 2 | $6.90 | https://www.mcmaster.com/90576A102 | Lock nuts for attaching caster to chassis
24’’ x 36’’ - 1/8’’ Thick Clear Acrylic Sheet | $27.80 | 5 | $139.00 | http://a.co/d/gHgLLsl | Acrylic sheet to laster cut for robot chassis.
24’’ x 24’’ - 1/16’’ Thick Clear Acrylic Sheet | $19.99 | 7 | $139.93 | http://a.co/d/isk6QyS | Acrylic sheet to be laser cut for battery holder and charging plate.
8’’ M-M Micro USB to Micro USB | $5.06 | 55 | $278.30 | http://a.co/d/02ey9tC | USB to connect the Raspberry Pi Zero to Teensy
DiGiYes Wireless Charging Receiver | $10.00 | 55 | $550.00 | http://a.co/d/eJUInFT | Wireless charging receiver (optional for non Robotarium use)
Lithium Ion Polymer Battery - 3.7v 2500mAh | $14.95 | 55 | $822.25 | https://www.adafruit.com/product/328 | Battery to power the robot.
Teensy 3.2 Microcontroller | $19.95 | 55 | $1097.25 | https://www.adafruit.com/product/2756 | Low level micro-controller
Raspberry Pi Zero W Basic Pack | $24.50 | 55 | $1347.50 | https://www.adafruit.com/product/3409 | High Level Processor
JST PH 2-Pin Cable - Female Connector 100mm | $0.75 | 55 | $41.25 | https://www.adafruit.com/product/261 | Power Cable Jumper for Raspberry Pi
Micro Metal Gear Motor with Encoder (100:1 gearing) | $11.50 | 110 | $1265.00 | https://www.dfrobot.com/product-1433.html | Motors for the robot.
Pololu Micro Metal Gearmotor Bracket Pair – Black | $4.99 | 55 | $274.45 | https://www.pololu.com/product/989 | Mount for securing motors to acrylic chassis
Pololu Wheel 32×7mm Pair – Black | $4.98 | 55 | $273.90 | https://www.pololu.com/product/1087 | Wheels that attach to the motors.
Pololu Carrier with Sharp GP2Y0A60SZLF Analog Distance Sensor 10-150cm, 5V | $12.17 | 385 | $4685.45 | https://www.pololu.com/product/2474 | IR Range Sensors
Tamiya Caster Ball | $5.95 | 28 | $166.60 | https://www.sparkfun.com/products/320 | Caster Ball to Balance Robot
SWITCH SLIDE SPST 500MA 125V | $1.30 | 55 | $71.50 | https://www.digikey.com/short/jfcbcq | Main Power Switch for Robot
CONN HEADER PH TOP 2POS 2MM | $0.17 | 55 | $9.35 | https://www.digikey.com/short/jfcjf3 | Power Jumper for Pi to Main Board
BERGSTIK HDR 14POS .100" DR SMT | $1.44 | 55 | $79.20 | https://www.digikey.com/short/jbdd3f | Header pins for underside of Teensy 3.2
Compression Spring | $2.00 | 165 | $330.00 | https://www.springsfast.com/part_detail_compression.php?part=C05-014-008 | Spring for pseudo suspension on the caster ball of the robot (avoids rattle)
Total |  |  | $12916.49

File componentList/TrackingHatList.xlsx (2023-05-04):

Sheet: Single Hat
Item | Price Per Item | Number Needed | Total Price | Order Link | Description
3/16’’ Aluminum F-F Threaded Hex Standoff | $0.46 | 4 | $1.84 | https://www.mcmaster.com/91780A523 (https://www.mcmaster.com/93505A466) | Aluminum stand off for spacing tracking hat from top plate.
1/2’’ 4-40 Screws | $1.75 | 0.06 | $0.10 | https://www.mcmaster.com/90272A110 | Attaching hat to robot and marker holder. Screws come in 100 pack bags
3/4’’ 4-40 Screws | $2.39 | 0.02 | $0.05 | https://www.mcmaster.com/90272A113 | Pearl marker holder.
1’’ 4-40 Screws | $3.09 | 0.02 | $0.06 | https://www.mcmaster.com/90272A115 | Pearl marker holder.
1 1/4’’ 4-40 Screws | $10.31 | 0.02 | $0.21 | https://www.mcmaster.com/90272A117 | Pearl marker holder.
4-40 Metal Lock Nut | $2.79 | 0.04 | $0.17 | https://www.mcmaster.com/90631A005 (https://www.mcmaster.com/93505A466) | Lock nuts to secure pearl marker holders.
24’’ x 24’’ - 1/16’’ Thick Clear Acrylic Sheet | $19.99 | 0.01176470588 | $0.24 | http://a.co/d/isk6QyS | Acrylic sheet to be laser cut for battery holder and charging plate.
Total |  |  | $2.67

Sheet: Multiple Hats
Number of Robots Required | 55
Item | Price Per Item | Number Needed | Total Price | Order Link | Description | Order Location Color
3/16’’ Aluminum F-F Threaded Hex Standoff | $0.46 | 220 | $101.20 | https://www.mcmaster.com/91780A523 | Aluminum stand off for spacing tracking hat from top plate.
1/2’’ 4-40 Screws | $1.75 | 4 | $7.00 | https://www.mcmaster.com/90272A110 | Attaching hat to robot and marker holder. Screws come in 100 pack bags
3/4’’ 4-40 Screws | $2.39 | 2 | $4.78 | https://www.mcmaster.com/90272A113 | Pearl marker holder.
1’’ 4-40 Screws | $3.09 | 2 | $6.18 | https://www.mcmaster.com/90272A115 | Pearl marker holder.
1 1/4’’ 4-40 Screws | $10.31 | 2 | $20.62 | https://www.mcmaster.com/90272A117 | Pearl marker holder.
4-40 Metal Lock Nut | $2.79 | 3 | $8.37 | https://www.mcmaster.com/90631A005 | Lock nuts to secure pearl marker holders.
24’’ x 24’’ - 1/16’’ Thick Clear Acrylic Sheet | $19.99 | 1 | $19.99 | http://a.co/d/isk6QyS | Acrylic sheet to be laser cut for battery holder and charging plate.
Total |  |  | $168.14

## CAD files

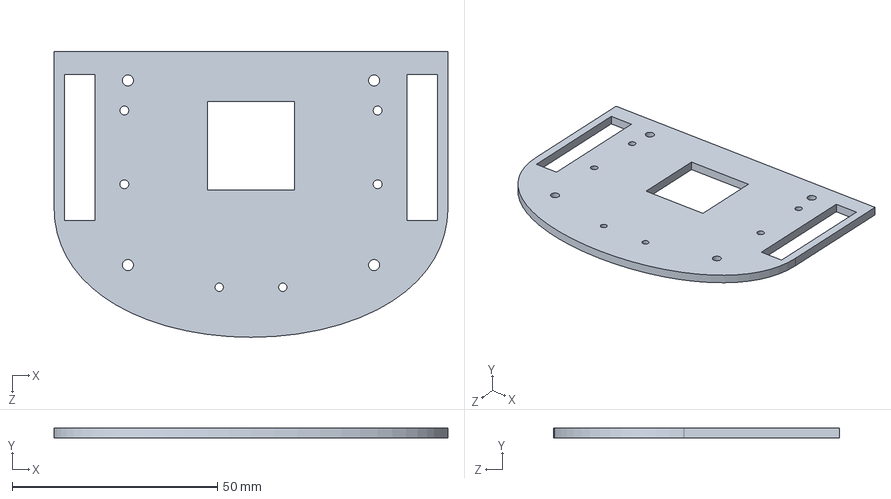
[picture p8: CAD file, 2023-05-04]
chassisDesign/pololuCasterDesign/main_plate_basic.SLDPRT
96.0 x 2.54 x 69.6 mm

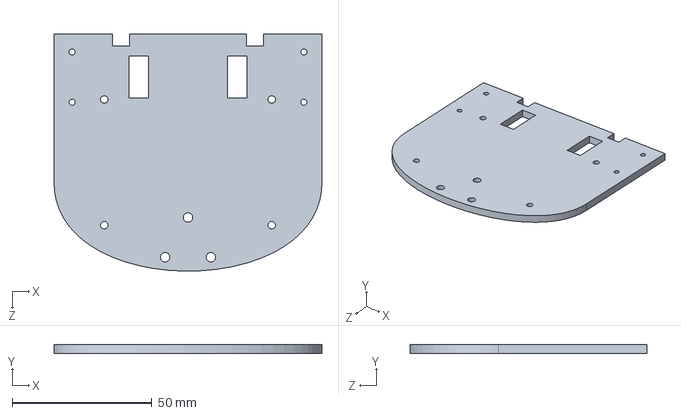
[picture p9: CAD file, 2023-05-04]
chassisDesign/zero4UDesign/main_plate_outside_wheels.SLDPRT
96.0 x 3.17 x 85.0 mm

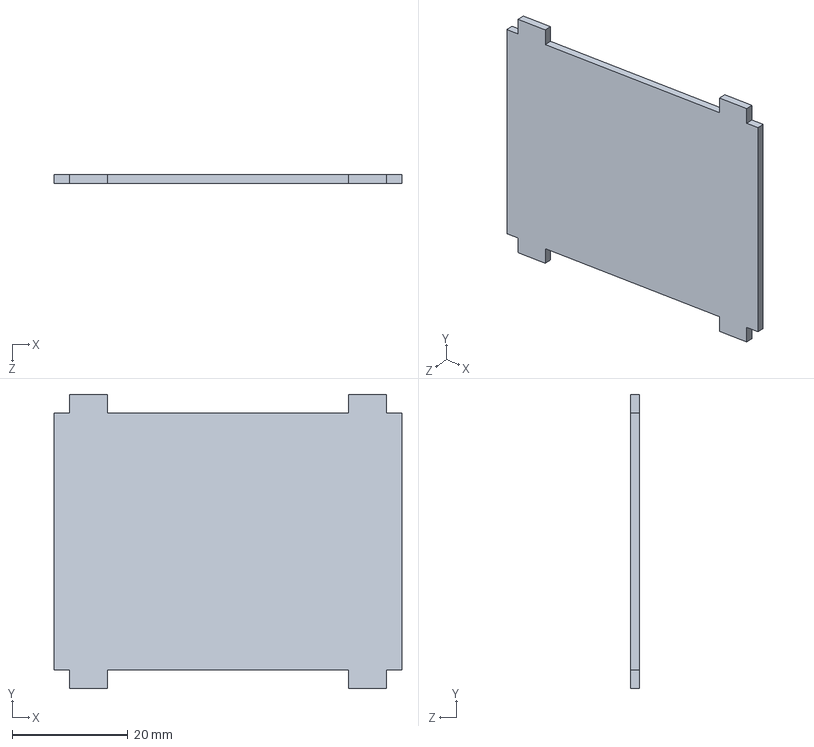
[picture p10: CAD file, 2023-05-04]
chassisDesign/tamiyaCasterDesign/back_sandwich.SLDPRT
60.0 x 50.7 x 1.59 mm

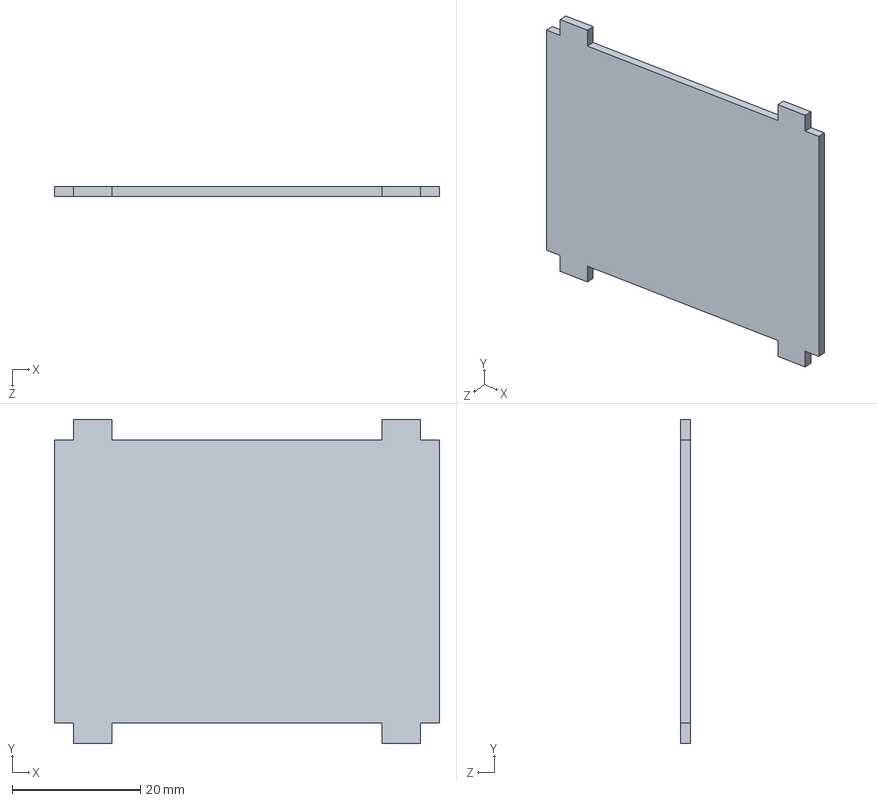
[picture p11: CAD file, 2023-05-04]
chassisDesign/zero4UDesign/inner_sandwich.SLDPRT
60.0 x 50.5 x 1.59 mm

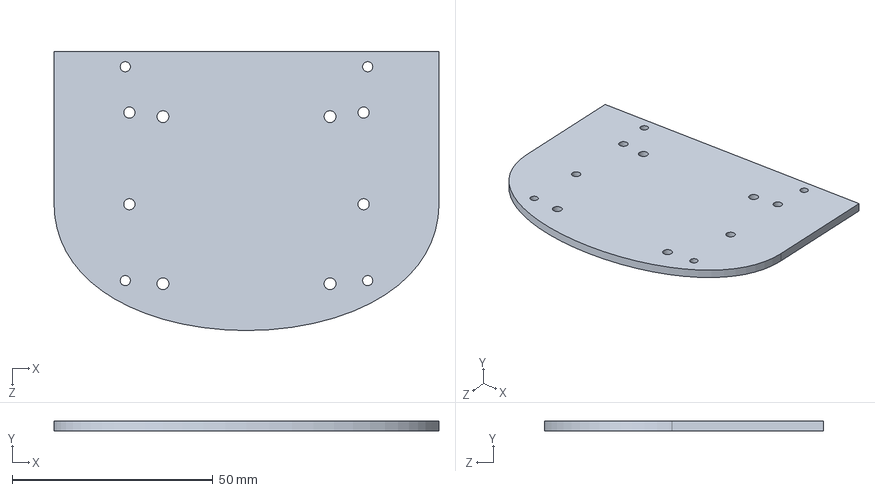
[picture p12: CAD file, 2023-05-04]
chassisDesign/pololuCasterDesign/top_plate.SLDPRT
96.0 x 2.54 x 69.6 mm

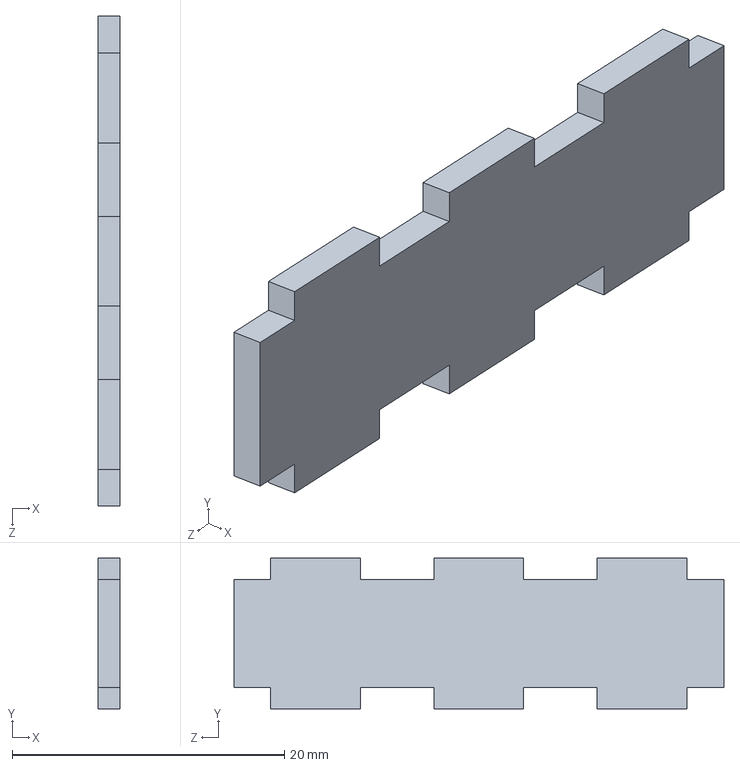
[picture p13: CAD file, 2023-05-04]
chassisDesign/tamiyaCasterDesign/battery_box_part.SLDPRT
1.59 x 11.1 x 36.0 mm

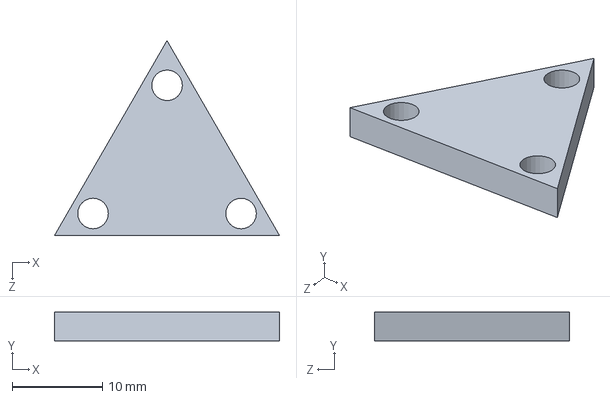
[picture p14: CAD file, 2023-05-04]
chassisDesign/tamiyaCasterDesign/caster_spacer.SLDPRT
25.0 x 3.17 x 21.7 mm

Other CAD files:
chassisDesign/pololuCasterDesign/main_plate.SLDPRT
chassisDesign/tamiyaCasterDesign/main_plate_outside_wheels.SLDPRT
chassisDesign/pololuCasterDesign/top_plate_basic.SLDPRT
chassisDesign/tamiyaCasterDesign/top_plate_outside_wheels.SLDPRT
chassisDesign/zero4UDesign/top_plate_outside_wheels.SLDPRT
chassisDesign/zero4UDesign/outer_sandwich.SLDPRT
chassisDesign/pololuCasterDesign/gritsBotX.SLDDRW

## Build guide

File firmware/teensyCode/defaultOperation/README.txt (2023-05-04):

Default operation simply moves the robot in response to JSON message commands. It also returns battery status information when requested from a JSON message command.

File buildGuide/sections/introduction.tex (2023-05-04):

\section{Introduction}
\label{sec:intro}

The GRTISBot X is an inexpensive, differential drive robot developed by the Georgia Robotics and Intelligent Systems Laboratory (GRITS Lab) in the Fall of 2018. It was originally designed for general multi-agent robot applications on the Robotarium \cite{robotarium,robotariumWebsite} to replace the GRITSBot \cite{GRITSBot}. The GRITSBot X is a small, versatile robot that can be deployed alone or in groups for hobby use, educational purposes, or research applications. The robot itself is almost entirely constructed of off the shelf components with a custom laser cut acrylic chassis and printed circuit board (PCB) being the only exception. The files to create these custom components (or have them fabricated externally) are found in the Github repository {\textcolor{red}{NEED CITATION WHEN MADE}}. A completed GRITSBot X can be seen in \cref{fig:GRITSBotX_Full}.

\begin{figure}[!h]
\centering

\caption{The completely assembled GRITSBot X with pearl tracking markers.}
\label{fig:GRITSBotX_Full}
\end{figure}

This document is meant as a step by step guide to construct a GRITSBot X with detailed photos and descriptions of required parts. The sections below will be broken into a short list of assembly steps with more detailed instructions on each step in the subsequent subsections. The details of each step are also linked if you are viewing the PDF on a computer. If this is your first build of the GRITSBot X, it is highly recommended that the detailed sections are read in full. The members of the GRITS Lab are glad you have chosen to take the time to build this robot. If you have any questions feel free to reach out to the contact at the top of this guide.

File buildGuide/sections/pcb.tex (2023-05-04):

\section{Printed Circuit Board Assembly}
\label{sec:pcb}

An eagle file has been provided on the github for the main printed circuit board (PCB) of the GRITBot X. This guide assumes that the board has been sent out for fabrication and  assembly. This means the external company that fabricated the board has also placed the surface mount components as seen in \cref{fig:pcbPlain}. You can have this done at a variety of vendors, we have used Circuithub \cite{circuithub} and Advanced Circuits \cite{advancedCircuits} in the past. The rest of this section will consider the through hole components that have yet to be placed.

%PCB Picture straight from Circuithub.
\begin{figure}[t]
\centering

\caption{The main circuit board of the GRITSBot X after fabrication and partial assembly. This is the assumed starting point for PCB assembly.}
\label{fig:pcbPlain}
\end{figure}
%End PCB Picture straight from Circuithub
\vspace{1cm}
\noindent\textbf{\large{Assembly of Piggyback Boards}}\\

 A piggyback board is essentially a PCB that connects to another PCB. The GRITSBot X leverages two of these pre-made boards, the Teensy 3.2 microcontroller \cite{teensy} and the Pololu Carrier with Sharp GP2Y0A60SZLF Analog Distance Sensor \cite{pololuDistance}. The Teesny 3.2 is a microcontroller that handles the low level actuator control and sensor acquisition of the GRITSBot X.  The Pololu Sharp IR distance carrier enables the easy use of the GP2Y0A60SZLF range sensor.
 
 \subsection{Teensy 3.2}
 
 \subsubsection{Assembly Steps}
 
 \begin{enumerate}
 \item Gather the required materials (\cref{sec:teensyMaterials}).
 \item Solder the first set of male breakaway headers to the board leaving the left side unpopulated (\cref{sec:teensyFirstSolder}). 
 \item Mount and solder the surface mount header pins to the underside of the Teensy (\cref{sec:teensySecondSolder}).
 \item Finish soldering the header pins to the Teensy by populating the left side (\cref{sec:teensyFinalSolder}).
 \end{enumerate}
 
 %%% Teensy Materials Subsection
 \subsubsection{Required Materials}
 \label{sec:teensyMaterials}
 
 First, gather the required materials. The Teensy 3.2 microcontroller from PJRC, \cref{fig:teensyTB}, should come with the board and a $1 \times 36$ male breakaway header pin. If your Teensy did not come with male breakaway header pins, they are extremely inexpensive and can be purcased at a variety of locations.
 
 %Teensy 3.2 Picture.
\begin{figure}[h!]
\centering

\caption{The Teensy 3.2 microcontroller top (\textbf{left}) and bottom (\textbf{right}) view.}
\label{fig:teensyTB}
\end{figure}
%End Teensy 3.2 Picture
 
 First, break the $1 \times 36$ breakaway header into smaller sections as described in \cref{tab:teensyBreakaway}. You may notice the number of male headers here totals 37 not the 36 provided with the board. You may either find a spare (recommended) or not populate the VUSB through hole.
 
  %Begin Teensy Part Table
 \begin{table}[h!]
 \centering
\begin{tabular}{ll}
\rowcolor[HTML]{C0C0C0} 
Number Required & Breakaway Dimension \\
2               & $1 \times  14$              \\
\rowcolor[HTML]{C0C0C0} 
1               & $1 \times 5$               \\
1               & $1 \times 3$               \\
\rowcolor[HTML]{C0C0C0} 
1               & $1 \times 1$              
\end{tabular}
\caption{The dimensions of the male breakaway headers needed to assemble the Teensy 3.2 microcontroller. \label{tab:teensyBreakaway}}
\end{table}
 %End Teensy Part Table

We also require the surface mount pins available on the underside of the Teensy 3.2 as seen in the right side of \cref{fig:teensyTB}. This requires a 14 position surface mount header and broken perforated board pictured in the bottom of \cref{fig:teensyParts}. Now that we have all the parts we can begin soldering this board together.

 %Teensy Parts Picture
\begin{figure}[h!]
\centering

\caption{The parts needed to solder header pins to the Teensy 3.2 microcontroller.}
\label{fig:teensyParts}
\end{figure}
%End Teensy Parts Picture

%%%First Solder Pass Subsection (Male Headers)
\subsubsection{Creating Perpendicular Solder Points and the First Solder Pass}
\label{sec:teensyFirstSolder}

Using the main PCB as a guide, slide all the male breakaway headers (excluding the surface mount ones) into the PCB (\cref{fig:teensyMaleHeader}) and place the Teensy 3.2 on top (\cref{fig:teensyMountedMaleHeader}) as shown in \cref{fig:teensyFirstPass}. \textbf{\textcolor{red}{Before soldering}}, observe the proximity of the header pads to the main processor chip (big black square) connections. When soldering be very carful not to accidentally solder or bridge these connections. It is best to keep the iron and solder being applied on the outside perimeter of the board. At this point solder all of the header pins on the Teensy {\textcolor{red}{\textbf{except}}} the left side headers as seen in \cref{fig:teensyFirstSolder}. It is extremely important that the left side header pins be left unpopulated for now so there is enough room for the soldering iron to attach the surface mount headers in the next step.

 %Male headers in PCB picture
\begin{figure}[h!]
\centering
\subfloat[\label{fig:teensyMaleHeader}]{}
\hfill
\subfloat[\label{fig:teensyMountedMaleHeader}]{}\\
\subfloat[\label{fig:teensyFirstSolder}]{}
\caption{Creating perpendicular solder points for the Teensy 3.2 using the GRITSBot X main PCB.}
\label{fig:teensyFirstPass}
\end{figure}
%End Male headers in PCB picture

%%%Second Solder Pass Subsection (Surface Mount)
\subsubsection{Soldering the Surface Mount Headers}
\label{sec:teensySecondSolder}

Now that the majority of the male headers have been soldered in place, we must now attach the surface mount headers. A major challenge here is mounting them so they align with the rest of the headers or the Teensy will not be able to fit into the main PCB of the GRITSBot X. To do this we will use the broken piece of perforated board, the 14 position surface mount header pins, and the Teensy that has been soldered so far (seen in \cref{fig:teensyMaterialsSecondSolder}).

 %Teensy Materials Surface Mount Picture
\begin{figure}[h!]
\centering

\caption{The 14 position surface mount header, perforated board, and Teensy required to make the underside pins of the Teensy accessible.}
\label{fig:teensyMaterialsSecondSolder}
\end{figure}
%End Teensy Materials Surface Mount Picture  

Insert the surface mount header pins into the broken perforated board leaving at least 6 pins exposed as seen in \cref{fig:surfaceHeaderPerf}. Note, in this picture 8 pins are left exposed. Inset the Teensy into the same perforated board such that the surface pads of the Teensy are aligned with the surface mount header pins as seen in \cref{fig:surfaceHeaderPerfTeensy}. Make sure the surface mount headers are pressed into the Teensy pads and solder the first few pad, header connections into place with the perforated board keeping them aligned. After the solder cools, remove the perforated board and solder the rest of the connections. Upon completion your board should resemble that in \cref{fig:surfaceHeaderTeensy}.

 %Male headers in PCB picture
\begin{figure}[h!]
\centering
\subfloat[\label{fig:surfaceHeaderPerf}]{}
\hfill
\subfloat[\label{fig:surfaceHeaderPerfTeensy}]{}\\
\subfloat[\label{fig:surfaceHeaderTeensy}]{}
\caption{Aligning and soldering the surface mount headers for the Teensy.}
\label{fig:teesnySurfaceHeaderPerf}
\end{figure}
%End Male headers in PCB picture

%%%Second Solder Pass Subsection (Surface Mount)
\subsubsection{Finishing Soldering the Teensy}
\label{sec:teensyFinalSolder}

To finish the Teensy, insert it back into the main GRITSBot X PCB as a guide and solder the remaining male header pins on the left side of the board. \textbf{\textcolor{red}{Again, before soldering}}, observe the proximity of the header pads to the main processor chip (big black square) connections. When soldering be very careful not to accidentally solder or bridge these connections. It is best to keep the iron and solder being applied on the outside perimeter of the boards. After making the final solder connection, you're done! The top and bottom of the finished Teensy should look like \cref{fig:teensyFinished}. The Teensy microcontroller is ready to be permanently attached to the main PCB of the GRITSBot X. Check it for bridged connections or poor solder joints. For now, take the Teensy out of the main PCB of the GRITSBot and set it aside to be attached later.

 %Teensy Materials Surface Mount Picture
\begin{figure}[h!]
\centering

\caption{The Teensy with headers attached.}
\label{fig:teensyFinished}
\end{figure}
%End Teensy Materials Surface Mount Picture  

\subsection{Pololu Carrier with Sharp GP2Y0A60SZLF Analog Distance Sensor}

 \subsubsection{Assembly Steps}
 
 \begin{enumerate}
 \item Gather the required materials (\cref{sec:sharpMaterials}).
 \item Cut the IR sensor down to size (\cref{sec:cutSharp}).
 \item Solder the right angle male header pins (\cref{sec:sharpSolder}).
 \end{enumerate}
 
  %%% Sharp Materials Subsection
 \subsubsection{Required Materials}
 \label{sec:sharpMaterials}
 
 Pololu provides the sensor attached to a custom PCB, male breakaway header pins, and right angle breakaway male header pins as seen in \cref{fig:sharpMaterials}. Only the sensor and right angle breakaway male header pins are needed for this. This means the normal breakaway header pins may be used for other projects (or for populating the VUSB pin on the Teensy).
 
 The GRITSBot X uses seven of these sensors so we require seven of these kits and soldering described below will have to be performed on each of the sensors.
 
 %Sharp Materials Picture
\begin{figure}[h!]
\centering

\caption{The materials required to assemble the Sharp infra-red piggyback board.}
\label{fig:sharpMaterials}
\end{figure}
%End Sharp Materials Picture  

 \subsubsection{Cutting the Pololu Carrying Board}
 \label{sec:cutSharp}
 
 The Pololu carrying board, that supports the Sharp IR sensor used on the robot, comes with a screw mounting hole that we do not use for this robot. In order to keep the robot's center of gravity low, we must cut the excess PCB used for a screw mount. The aim is to make a flat cut right below the plastic black sensor casing where the screw hole is. There are a few ways to do this. This guide will discuss three options with their drawbacks,
 
 \begin{itemize}
 \item Use a pair of scizzors to cut the boards. This is the most time efficient and safe way to do this. The drawback is that it can be hard on your hands so wear gloves or take breaks between large amounts of cuts (if you are mass producing).
 \item Use a box cutter to slice at each side and then snap the board along the weakened line. This is agin relatively safe but you have a higher chance of cutting yourself. This method is also rather time consuming.
 \item Use a dremel or other machine cutter to cut the board. This method works but is not recommended unless the above two fail. {\textcolor{red}{NOTE}}: this will create dust that is possibly hazardous so wear breath protection. You should also place the sensor into a vice or some other type of holder. Do not hold it in your hand as the dremel will most likely catch and you can BADLY hurt yourself.
 \end{itemize} 
 
  %Sharp Cut Picture
\begin{figure}[h!]
\centering

\caption{The Sharp IR sensor after being cut to size.}
\label{fig:cutSharp}
\end{figure}
%End Sharp Cut Picture

After cutting the sensor the sensor should look simlar to the one pictured in \cref{fig:cutSharp}.  
 
 %%% Sharp Soldering Subsection
 \subsubsection{Soldering the Header Pins}
 \label{sec:sharpSolder}
 
 Soldering the right angle breakaway header pins to this boards is relatively straight forward. However, it is important to make these solder joints as perpendicular to the board as possible. To do this, first insert the long straight section of the breakaway header through the back of the board such that the right angle pins are on the opposite side of the sensor (seen in \cref{fig:sharpHeaders}). Solder one pin connection. Lay the sensor face down and heat that connection while pushing the pins you are not heating (so you don't burn yourself) stright into the board such that they become perpendicular with the board. \textbf{\textcolor{red}{Careful}} not to leave the heat on this pin too long or you will melt the plastic holding it and cause misalignment of the right angle pins. If this happens the IR sensor cannot be inserted into the GRITSBot X's main PCB.
 
 After aligning the pins properly using the single solder point. Solder the rest of the pins and cut the excess with a wire cutter. The resulting sensor should look like \cref{fig:sharpFinished}.
 
%Male headers in PCB picture
\begin{figure}[h!]
\centering
\subfloat[\label{fig:sharpHeaders}]{}
\hfill
\subfloat[\label{fig:sharpFinished}]{}\\
\caption{Sharp infra-red distance sensor with headers properly attached.}
\label{fig:teesnySurfaceHeaderPerf}
\end{figure}
%End Male headers in PCB picture

\subsection{Populating the GRITSBot X Main PCB}
\label{sec:mainPCB}

 \subsubsection{Assembly Steps}
 
 \begin{enumerate}
 \item Gather the required materials (\cref{sec:mainPCBMaterials}).
 \item Solder the Teensy microcontroller, JST PH 2-Pin male header, and power switch (\cref{sec:solderTopComponents}).
 \item Solder the motor jumper cables (\cref{sec:solderMotorJumper}).
 \item Solder the IR sensors (\cref{sec:solderIRSensor}).
 \end{enumerate}
 
 \subsubsection{Required Materials}
 \label{sec:mainPCBMaterials}

All of the parts should now be ready to populate the main PCB of the GRITSBot X. To start we will add the Teensy 3.2, JST PH 2-Pin male header (power jumper for the Raspberry Pi), and main power switch. The materials you will need are pictured in \cref{fig:mainPCBFirstPass}.

%First Board Parts
\begin{figure}[h!]
\centering

\caption{The materials for the first solder pass of the main PCB of the GRITSBot X.}
\label{fig:mainPCBFirstPass}
\end{figure}
%End First Board Parts

\subsubsection{Soldering the Top Through Hole Components}
\label{sec:solderTopComponents}

To start, first solder the Teensy into the main board (into the only spot where it fits). Make sure the Teensy is parallel with the main PCB of the GRITSBot X. To do this, lightly press the main chip of the Teensy into the main PCB. If this is not done, the connecting USB wire between the Teensy and Raspberry Pi (that will be added later) will not fit.

Next, place the ST PH 2-Pin male header (power jumper for the Raspberry Pi). It should be placed to the lower right of Teensy. The three openings on the side (meant for latching the female wire) should be facing the flat side of the board. You may have to press relatively hard as the tolerance of the drill for the main PCB may not be wide enough.

Finally, place the switch into the board (in the large holes to the left of the Teensy. Make sure the switch is facing the outside of the board and apply a large amount of solder. After finishing this, your board is ready to go minus the motors. Make sure all your solder connections are good and there are no cold joints or insufficient wetting. \cref{fig:mainPCBNoMotors} shows the top and bottom view of a completed board.

%First Populate Board
\begin{figure}[h!]
\centering

\caption{The GRITSBot X main PCB after mounting the Teesny microcontroller, JST PH 2-pin male header, and power switch.}
\label{fig:mainPCBNoMotors}
\end{figure}
%End First Populate Board

\subsubsection{Soldering the Motor and Encoder Leads}
\label{sec:solderMotorJumper}

The next parts to solder are the motor leads. This guide assumes you have purchased the micro metal gear motors with encoders attached from DFRobot. The row of six through holes correspond to the encoder attachments found on the DFRobot micro-metal gear motor. However, these pins are typically found in all quadrature shaft-encoders. From the top (curved edge) of the board to the bottom on both sides, the pins are: motor lead 1, ground, encoder output channel 1, encoder output channel 2, 5 volts, and motor lead 2. Make sure when soldering these they align with your motors correctly. This guide does not trim the motor leads shipped from DFRobot with the motors and instead coils the excess inside the robot. If you want you may cut the wire down to a smaller size but the stranded wire may be hard to keep from fraying out into a short when all six leads are attached. The wires connecting these motor leads are very small and can be tricky to attach without leaving too much excess exposed wire (which can lead to a short). A trick to make attaching these easier is to fill the through holes with solder and then heat the individual pad and insert the motor lead through the liquid solder. This allows you to slightly press and melt the insulation of the wire lead into the board which leaves no exposed metal. After attaching the motor leads, the bottom of the board should look like \cref{fig:finishedPCB}.

%Final Populate Board
\begin{figure}[h!]
\centering

\caption{The GRITSBot X main PCB after mounting the motor leads.}
\label{fig:finishedPCB}
\end{figure}
%End Final Populate Board

\subsubsection{Soldering the IR Sensors}
\label{sec:solderIRSensor}

Finally we will attach the IR sensors around the perimeter of the main PCB. Hang the sensors on the GRITSBot X main PCB such that the sensor hangs below the board (the side with the motor cables). To solder this, it is easier to solder the the pins from the angled side first and let the capillary action pull the solder through. You will also want to solder one pin and make sure the sensor is perpendicular to the main PCB. After the sensor is perpendicular, solder the other four pins and continue to populate the other six sensor slots.

\subsection{Wire Leads to the Raspberry Pi Zero W}
\label{sec:raspberryPiLeads}
To compliment the Teensy microcontroller on the main PCB of the GRITSBot X, the robot also uses a Raspberry Pi Zero W. This board is powered through the GPIO pins of the board. To achieve this solder the JST PH 2-Pin Cable - Female Connector to pin numbers 4 and 6 where 4 is the positive lead and 6 is the ground lead. Make sure this connection is donw with the correct polarity, if it does not you will destroy the Raspberry Pi Zero W.

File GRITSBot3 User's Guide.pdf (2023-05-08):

# GRITSBot 3.0

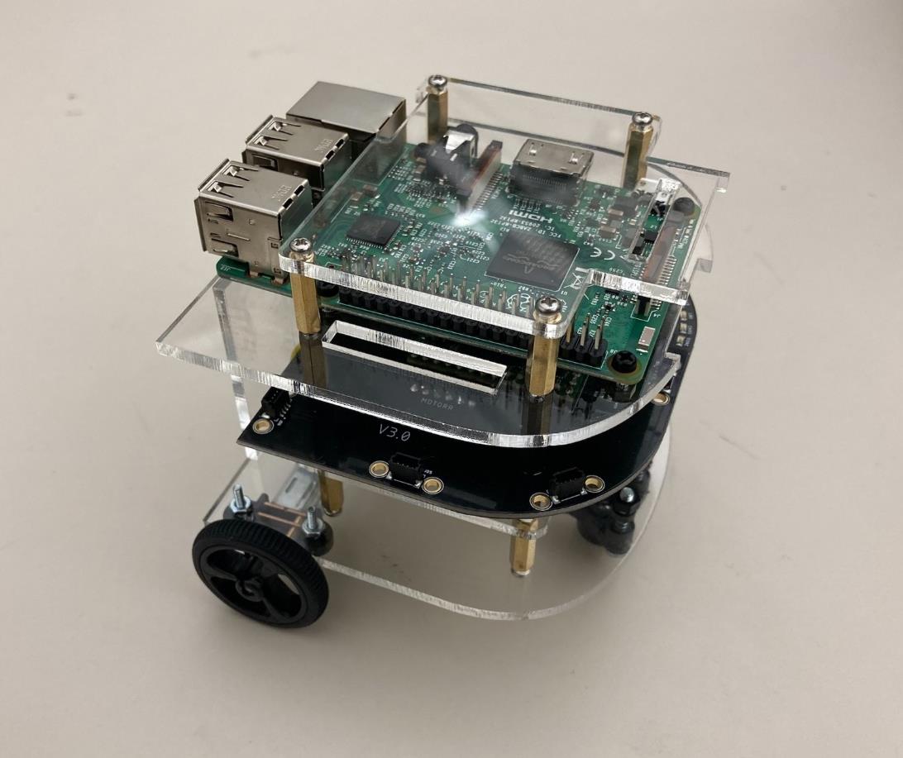
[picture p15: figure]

# User’s Guide

Paden Davis, Maxwell Chen, Nathan Yam

Dr. Sean Wilson, Dr. Samuel Coogan

May 4, 2023

## Table of Contents

2.9 I

## 1 Purpose

The purpose of this document is to explain the general design elements, assembly, and usage of the GRTISBot 3.0 robot.

## 2 Printed Circuit Board (PCB)

The printed circuit board (PCB) houses the majority of the electronics on the robot and features circuitry for power and sensors. Some of the circuitry is taken from the GRITSBot 2.0 PCB while other components are copied and modified versions of circuitry from breakout boards.

This section will detail the core circuitry of the GRITSBot 3.0 PCB.

### 2.1 On/Off Switch

The On/Off switch turns on and off the 5V and 6V power circuits of the robot. The On/Off switch has no connection to the charging circuitry.
2.2 | Status LEDs
Status LED | Description
PWR | On when On/Off switch is on and receiving power from battery/charger
LBO | Low battery indicator
CHRG | On when battery is charging or only charger connected.
DONE | On when batter is done charging.
2.3 | 5V Regulation
The 5V Regulation circuitry is taken and modified from Adafruit’s PowerBoost 1000C board. (https://www.adafruit.com/product/2465)

The circuitry takes power from the battery/charger and regulates it to 5V to power the Teensy, motor encoders, and motor driver.

### 2.4 6V Regulation

The 6V Regulation circuitry is taken from the GRITSBot 2.0 PCB.

The circuitry takes power from the battery/charger and regulates it to 6V for motor power.

### 2.5 Charging Circuitry

The charging circuitry is taken and modified from Adafruit’s PowerBoost 1000C board. (https://www.adafruit.com/product/2465)

The circuitry handles charging the robot battery and load-sharing between charger and battery.

### 2.6 Power Sensor

The power monitor is taken and modified from Adafruit’s INA260 Breakout Board. (https://www.adafruit.com/product/4226)

The INA260 power sensor is wired in series with the VBAT line directly after the charging circuitry and measures VBAT voltage/current and power usage.

If undesired, the PCB features pads for a jumper on the VBAT line to bypass the power sensor.

### 2.7 Teensy 4.0

The Teensy 4.0 (https://www.pjrc.com/store/teensy40.html) is a low-level microcontroller board that handles sensor and motor driver communications and control.

The Teensy takes in 5V and provides 3.3V for sensor power. The Teensy can be connected to microUSB for programming.

WARNING: There is potential for damage to the 5V regulation circuitry if the Teensy is connected to microUSB without battery/charger power. The cause is unknown at the moment but may be due to pre-biasing the output of the TPS61030 chip. Ensure that the robot is fully powered through battery/charger first before connecting the Teensy with microUSB that has external power.

### 2.8 H-Bridge Motor Driver

The H-Bridge Motor Driver takes power from 5V regulation and uses 6V for motor power. The driver is controlled by the Teensy.

### 2.9 I 2C Mux and Qwiic Connectors

The I²C is taken and modified from Sparkfun’s Qwiic Mux Breakout. (https://www.sparkfun.com/products/16784)

The GRITSBot 3.0 features seven distance sensors (https://www.adafruit.com/product/3317) with the same, unmodifiable I

2C address, so I

2C
mux circuitry is needed to properly access all of them.

The GRITSBot 3.0 PCB includes Qwiic connectors for wiring to the distance sensors and holes for distance sensor mounts.

### 2.10 Inertial Measurement Unit (IMU)

The I²C is taken and modified from Adafruit’s BNO055 Breakout Board. (https://www.adafruit.com/product/2472)

### 2.10 Pi Power & Communication

The PCB features 4 pins for providing power and serial communication to a Raspberry Pi.

## 3 Other Electronics and Components

This section details other electronics and components not on the PCB.

### 3.1 Distance Sensors

The GRITSBot 3.0 features seven Adafruit VL53L0X Time of Flight Distance Sensors. (https://www.adafruit.com/product/3317)

These distance sensors are connected to the PCB through a Qwiic cable and should be held using 3D-printed or laser-cut mount that can be bolted to the PCB.

### 3.2 Raspberry Pi

The GRITSBot 3.0 supports Raspberry Pi 3, 3b, 3b+, and 4.

The Raspberry Pi receives power from the Pi power pins on the PCB.

The Raspberry Pi serves as the main processor for the robot and communicates with the Teensy either through serial pins on the PCB or through USB

### 3.3 Pi Camera

The intended camera is a Raspberry Pi Camera V2, (https://www.raspberrypi.com/products/camera-module-v2/) but the GRITSBot 3.0 should support any camera that connects to a Raspberry Pi through the CSI connector.

### 3.4 Motors

The GRITSBot 3.0 uses two geared motors with encoders from DFRobot. (https://www.dfrobot.com/product-1433.html)

### 3.5 Battery

The GRITSBot 3.0 uses a 3.7V LiPo Battery from Adafruit (https://www.adafruit.com/product/328)

4 Assembly This section’s purpose is to walk through the steps involved in putting together a working

robot once all of the parts have been purchased or manufactured. To this end, the assembly process will require:

| • 1x Cut Acrylic Pieces • 2x 100:1 Motors • 1x Pack of two wheels • 1x Raspberry Pi (3B, 3B+, 4) • 7x Printed or machined distance sensor mounts • 7x ToF distance sensors • 7x 50mm or shorter Qwiic connector wires • 1x Front Caster Pack • 3x Small Caster Springs • 3x M3 Locknuts • 1x 3.7V Lipo Battery • 1x Teensy 4.0 board with pins soldered • 8x M2.5x15mm brass male to female standoffs • 4x M2.5x10mm nylon male to female standoffs • 4x M2.5x20mm nylon male to female standoffs • 4x M2.5 Locknuts • 4x M2.5x6mm Screws • 14x M2 Nylon Screws • 14x M2 Nylon Nuts • 4x 5cm Female to Female Jumper wires
4.1 | Assembly With an Assembled Circuit Board For this process, the steps are much simpler than without a circuit board, as all connections

except the motor connections will involve no soldering.

1. First, solder pins to the Teensy 4.0 if they have not already been soldered. Only the outer
| pins are necessary. Place the teensy into the circuit board putting the pins through the holes in the marked section on the silkscreen. Solder the teensy into the PCB. Clip off the pins on the bottom as low as possible without damaging the solder joints.
2. Next solder the motor connectors that come with each motor into the holes marked motorR
| and motorL respectively. The order of colors from the back side of the PCB goes Red, Black, Yellow, Green, Blue, then white, but please review the pinouts on the circuit board to ensure your connector colors are the same pattern.
3. Thread a 50mm or shorter Qwiic connector through the two upwards facing holes in the
| distance sensor mount. Plug the end exiting the front of the mount into a distance sensor, then mount the distance sensor using 2x M2x8mm Nylon screws and secure them with 2x M2 Nylon nuts. Repeat this 6 more times to obtain 7x mounted distance sensors with qwiic jumpers out the back of the mount.
4. Plug in each sensor to its Qwiic header on the PCB then, using more M2x8mm Nylon screws
| and nuts, screw each distance sensor mount into the PCB. Set the PCB to the side gently once all 7 are mounted.

5. Begin with the bottom acrylic plate. This one has two rectangular holes near the bottom side and three screw holes in the front. First, screw 4 M2.5x15mm brass standoffs into lock nuts through the four rectangularly spaced holes in the plate. Use pliers to hold them while screwing into the locknut if necessary.
6. Place the motors into their mounting brackets, making sure the flat panel at the end of the gearbox lines up with the edge of the bracket. Mount the brackets+motors to the bottom side (opposite side to the standoffs) of the plate using the screws provided with the brackets.
7. Place the wheels onto the motor shafts and make sure the wheels are angled straight and do not rub against the acrylic. Place the rubber ring on the outside to tighten them and lock them in place.
8. Thread the screws into the three holes on the caster, then place the caster springs and the 2mm spacers that come with the casters. Thread the end of the screws through the acrylic plate and secure them in place with 3x 3mm Locknuts.
9. Next place the battery plate (rectangle with rounded corners) onto the standoffs and attach 4x 10mm nylon standoffs through it into the brass standoffs of the bottom plate, securing it in place.
10. Onto this plate, place the battery. Then bring the circuit board with the teensy attached close. Ensure the power switch is switched off (towards the bottom of the board) then plug the motor connectors into their corresponding motor and the battery into the battery connector. You should see no lights turn on if the switch is correctly turned off.
11. Place the wires under the circuit board on top of the battery in a way that will hold them and hide their excess length, then place the circuit board on top of the standoffs from the battery plate. Thread M2.5x20mm standoffs into the battery plate standoffs through the holes in the PCB, holding the PCB in place and tightening it down.
12. Place 4x 5cm female to female jumper wires onto the Pi communication and power pins located next to the teensy location. From the top the colors recommended are Red, Black, Grey, White (For 5v, Gnd, Pi Tx, Pi Rx).
13. Screw the Raspberry Pi into the next plate, which looks similar to the bottom plate of the robot, using 4x M2x8mm nylon screws and nuts.
14. Thread the four wires through the slot on the right side of the plate and connect them to pins 2,3,4,5 (5v, Gnd, Tx, Rx) from the top on the right column of pins in the same order they are on the PCB.
15. Attach the plate to the standoffs from the PCB using 4x M2.5x15mm brass standoffs
16. Screw on the top plate using 4x M2.5x6mm screws.
17. Press fit the back plate into the grooves, and press fit the camera mount plate into the front slots. If using a camera, mount the CSI cable and thread it through the slot before attaching the top plate and press it under the top plate to keep the cable out of the way. Then mount the camera to the camera mount.

## 5 Uploading Code and Using the GRITSBot 3.0

WARNING: There is potential for damage to the 5V regulation circuitry if the Teensy is connected to microUSB without battery/charger power. The cause is unknown at the moment but may be due to pre-biasing the output of the TPS61030 chip. Ensure that the robot is fully powered through battery/charger first before connecting the Teensy with microUSB that has external power.

Upload the Teensy code found in the Github Gritsbot3/Firmware/teensyCode folder into the Teensy on the PCB through its microUSB port. Remember to have the board powered on and connected to the battery or charge port before plugging in the Teensy. This will require the Gritsbot3/Library folder to be placed in your Arduino libraries and the Arduino IDE set up to work with Teensy 4.0 which can be done following this guide. (https://www.pjrc.com/teensy/td_download.html)

Image the Raspberry Pi SD card with the image provided in the Github and plug that into the Pi. Power the Pi by turning on the Gritsbot and connect the Pi to a monitor through the HDMI port or USB C port depending on which version you are using. Plug a mouse and keyboard into the rear USB A ports and use this to complete the setup of the Pi and add a Wi-Fi connection. Additionally a Wi-Fi antenna can be connected into the rear USB A ports for better signal.

## 6 Future Changes

- The Robotarium code and raspberry Pi code currently do not support the additional sensors on the Gritsbot 3.0. These will need to be updated to allow the correct transfer of the data, as well as adding the ability to disable sensors through their registers to force them into sleep or deep sleep modes.
- To the PCB, we would like to add a timer circuit to power off the Pi for a certain length of time, then to power it back on. This would be useful to have while charging to charge as quickly and efficiently as possible.
- Add additional pinout headers to the PCB or a Qwiic header to allow extra I2C connections for breakout boards.
- Add additional power and short circuit protection to the PCB to prevent chip damage from powering the board through the Teensy or touching the board while it is powered.
- Move PCB components to improve ground/power connections and heat characteristics.
7 | Links and References
7.1 | Bill of Materials
GRITSBot 3.0 BOM: https://docs.google.com/spreadsheets/d/1fcbRilmKaX-AO9ylUm2N9gINN3ZsyIf4CjUE0T1iR2c/edit?usp=sharing (https://docs.google.com/spreadsheets/d/1fcbRilmKaX-AO9ylUm2N9gINN3ZsyIf4CjUE0T1iR2c/edit?usp=sharing)

### 7.2 GitHub

GRITSBot 3.0: https://github.com/Payday02/Gritsbot-3

GRITSBot 2.0 Hardware: https://github.com/robotarium/GRITSBot_hardware_design

### 7.3 Robotarium

Robotarium at Georgia Tech: https://www.robotarium.gatech.edu/

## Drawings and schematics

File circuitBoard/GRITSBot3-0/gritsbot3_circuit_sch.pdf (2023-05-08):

5V Regulation | 6V Regulation (Motors)
U$12 SW 7 | VIN 8 | EN 6

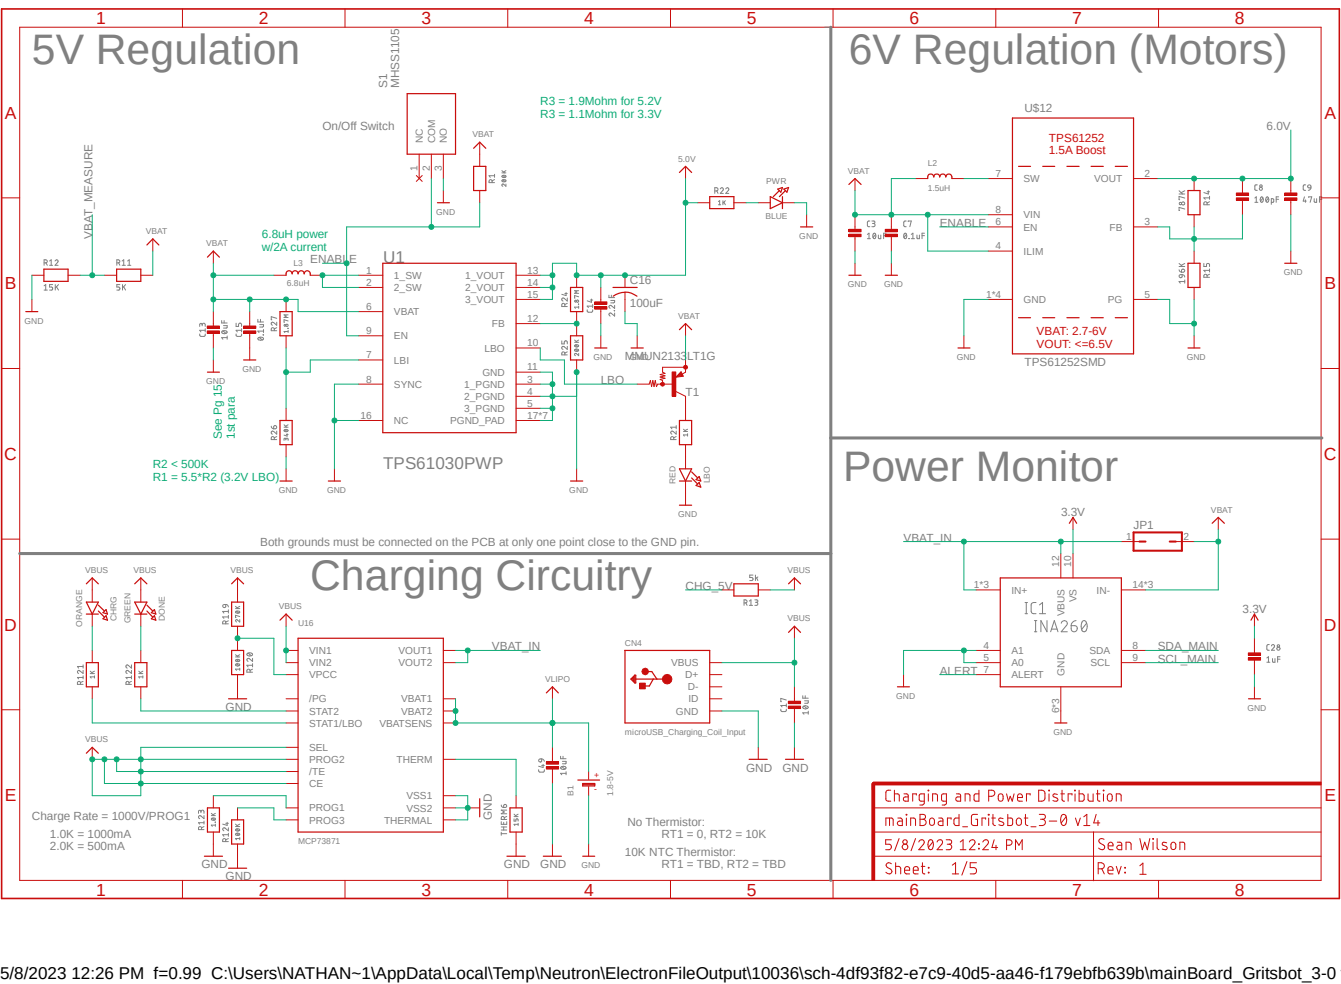
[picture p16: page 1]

VBAT MHSS¹¹⁰⁵

R1 = 5.5*R2 (3.2V LBO) See Pg 15 1st para

Both grounds must be connected on the PCB at only one point close to the GND pin.
Charging Circuitry

5/8/2023 12:26 PM f=0.99 C:\Users\NATHAN~1\AppData\Local\Temp\Neutron\ElectronFileOutput\10036\sch-4df93f82-e7c9-40d5-aa46-f179ebfb639b\mainBoard_Gritsbot_3-0 v14.sch (Sheet: 1/5)

A

A

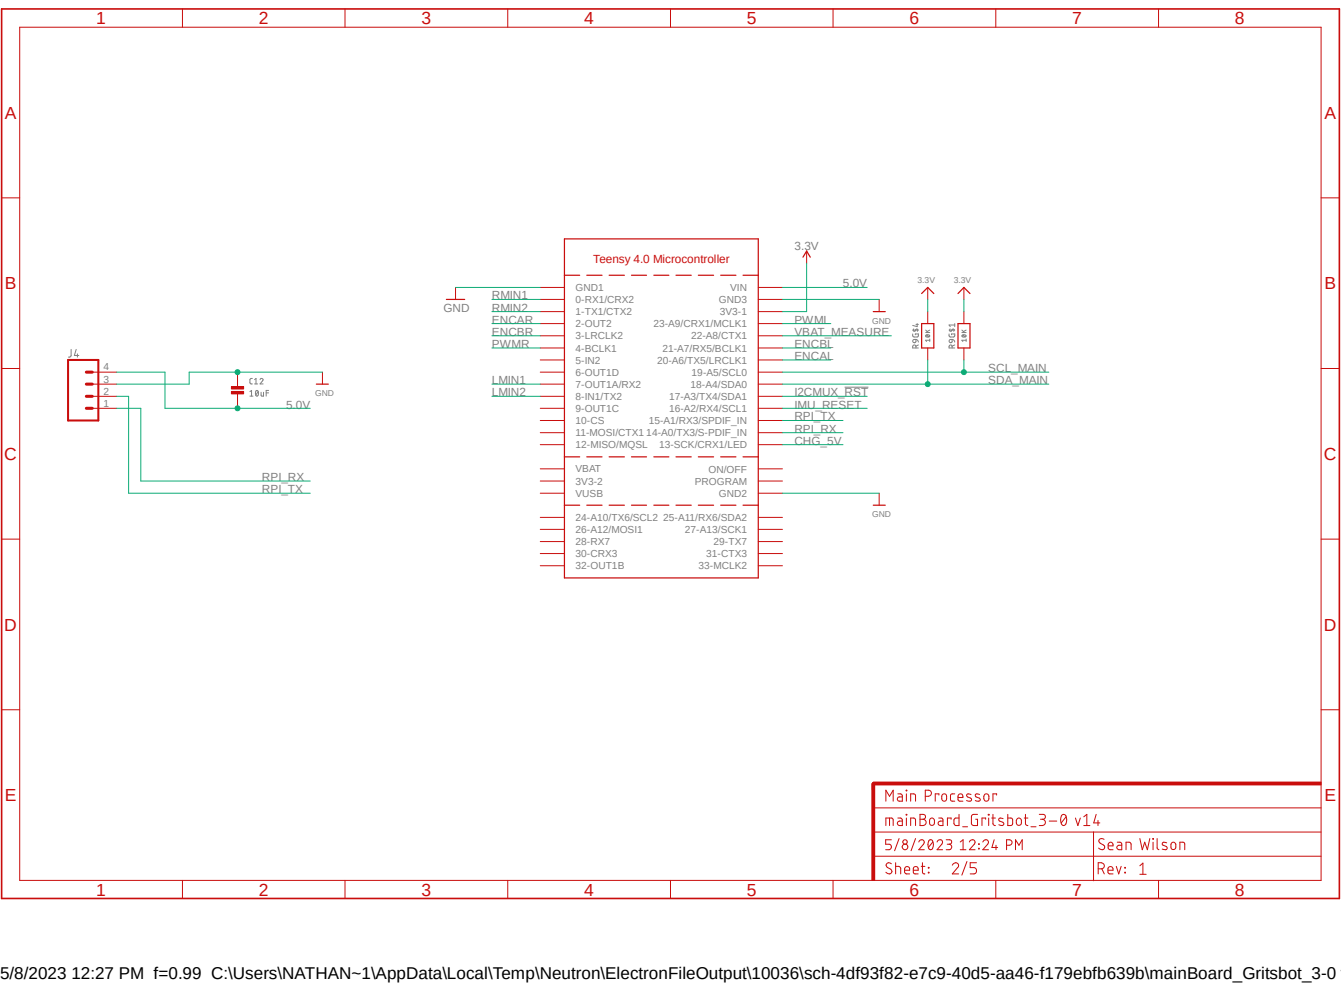
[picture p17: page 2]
GND; GND GND; 14-A0/TX3/S-PDIF_IN; 15-A1/RX3/SPDIF_IN; 16-A2/RX4/SCL1; 17-A3/TX4/SDA1; 18-A4/SDA0; 19-A5/SCL0; 20-A6/TX5/LRCLK1; 21-A7/RX5/BCLK1; 22-A8/CTX1; 23-A9/CRX1/MCLK1; 3-LRCLK2 4-BCLK1; 0-RX1/CRX2; 1-TX1/CTX2 VUSB GND1; GND2 GND3 VBAT; PROGRAM; ON/OFF; 6-OUT1D 7-OUT1A/RX2; 2-OUT2; 9-OUT1C 10-CS 11-MOSI/CTX1 12-MISO/MQSL 13-SCK/CRX1/LED; 3V3-1 VIN; 24-A10/TX6/SCL2 25-A11/RX6/SDA2; 26-A12/MOSI1; 27-A13/SCK1; 30-CRX3; 31-CTX3; 32-OUT1B; 33-MCLK2; LMIN1 LMIN2; PWML; PWMR; ENCAR ENCBR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

5/8/2023 12:27 PM f=0.99 C:\Users\NATHAN~1\AppData\Local\Temp\Neutron\ElectronFileOutput\10036\sch-4df93f82-e7c9-40d5-aa46-f179ebfb639b\mainBoard_Gritsbot_3-0 v14.sch (Sheet: 2/5)

A

A

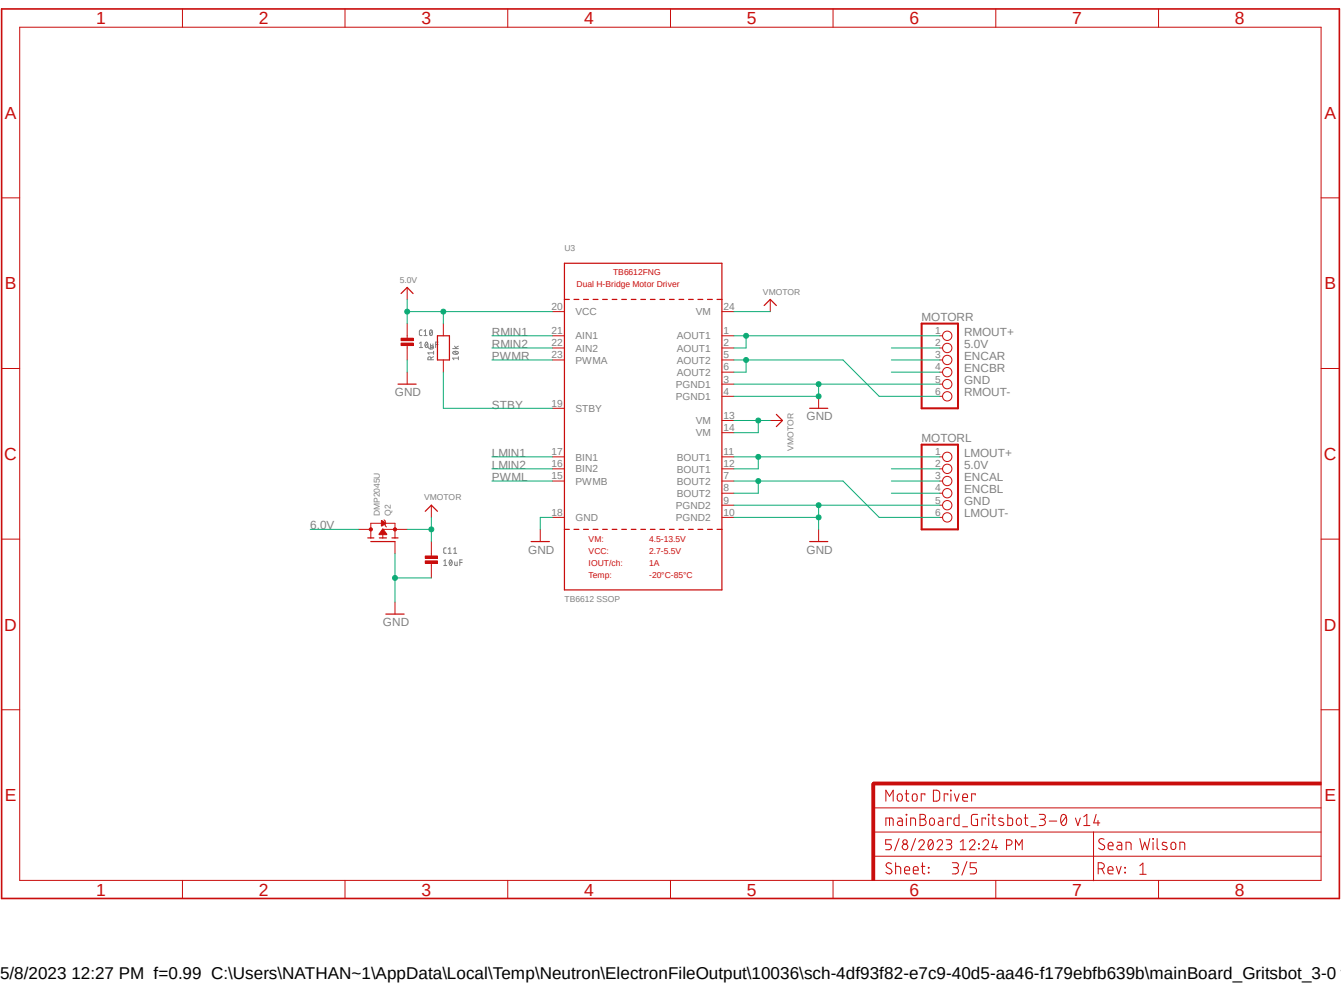
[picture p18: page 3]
TB6612 SSOP; VMOTORVMOTOR; GND; 5.0V DMP²⁰⁴⁵U; VMOTOR; U3VCC 20; STBY 19; AIN1 21; AIN2 22; PWMA 23; BIN1 17; BIN2 16; PWMB 15; GND 18; 24 AOUT1; 1 AOUT1; 2 AOUT2; 5 AOUT2; 6 PGND1; 3 PGND1; 14 BOUT1; 11 BOUT1; 12 BOUT2; 7 BOUT2; 8 PGND2; 9 PGND2; MOTORR; MOTORL 1 2 3 4 5; 6 RMIN1 RMIN2 PWMR; STBY; LMIN1 LMIN2 PWML; RMOUT+; RMOUT-; LMOUT+; LMOUT-; ENCAR ENCBR; ENCAL ENCBL; 8 TB6612FNG; Dual H-Bridge Motor Driver VM:; IOUT/ch:; Temp:; VCC:

5/8/2023 12:27 PM f=0.99 C:\Users\NATHAN~1\AppData\Local\Temp\Neutron\ElectronFileOutput\10036\sch-4df93f82-e7c9-40d5-aa46-f179ebfb639b\mainBoard_Gritsbot_3-0 v14.sch (Sheet: 3/5)

A

A

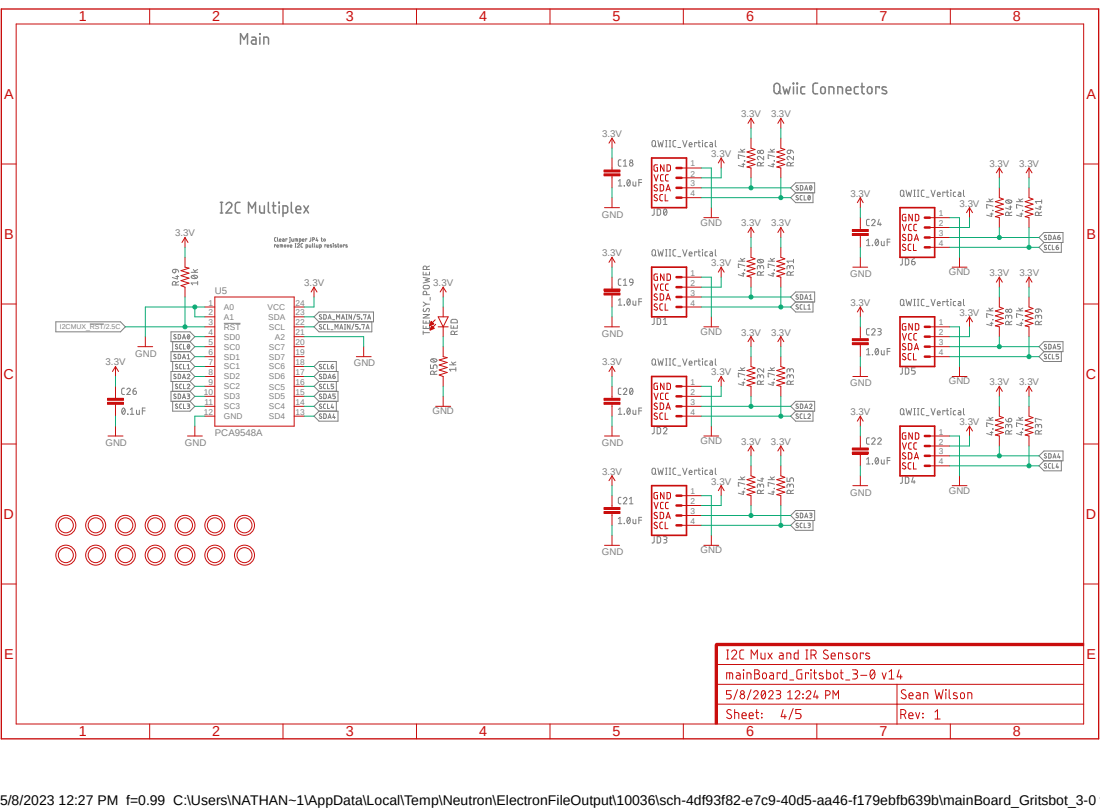
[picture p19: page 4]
GND; PCA9548A; SDA; 23 SCL; VCC; 21 RST 3; GND 12; I2CMUX_RST/2.5C

5/8/2023 12:27 PM f=0.99 C:\Users\NATHAN~1\AppData\Local\Temp\Neutron\ElectronFileOutput\10036\sch-4df93f82-e7c9-40d5-aa46-f179ebfb639b\mainBoard_Gritsbot_3-0 v14.sch (Sheet: 4/5)

A

A

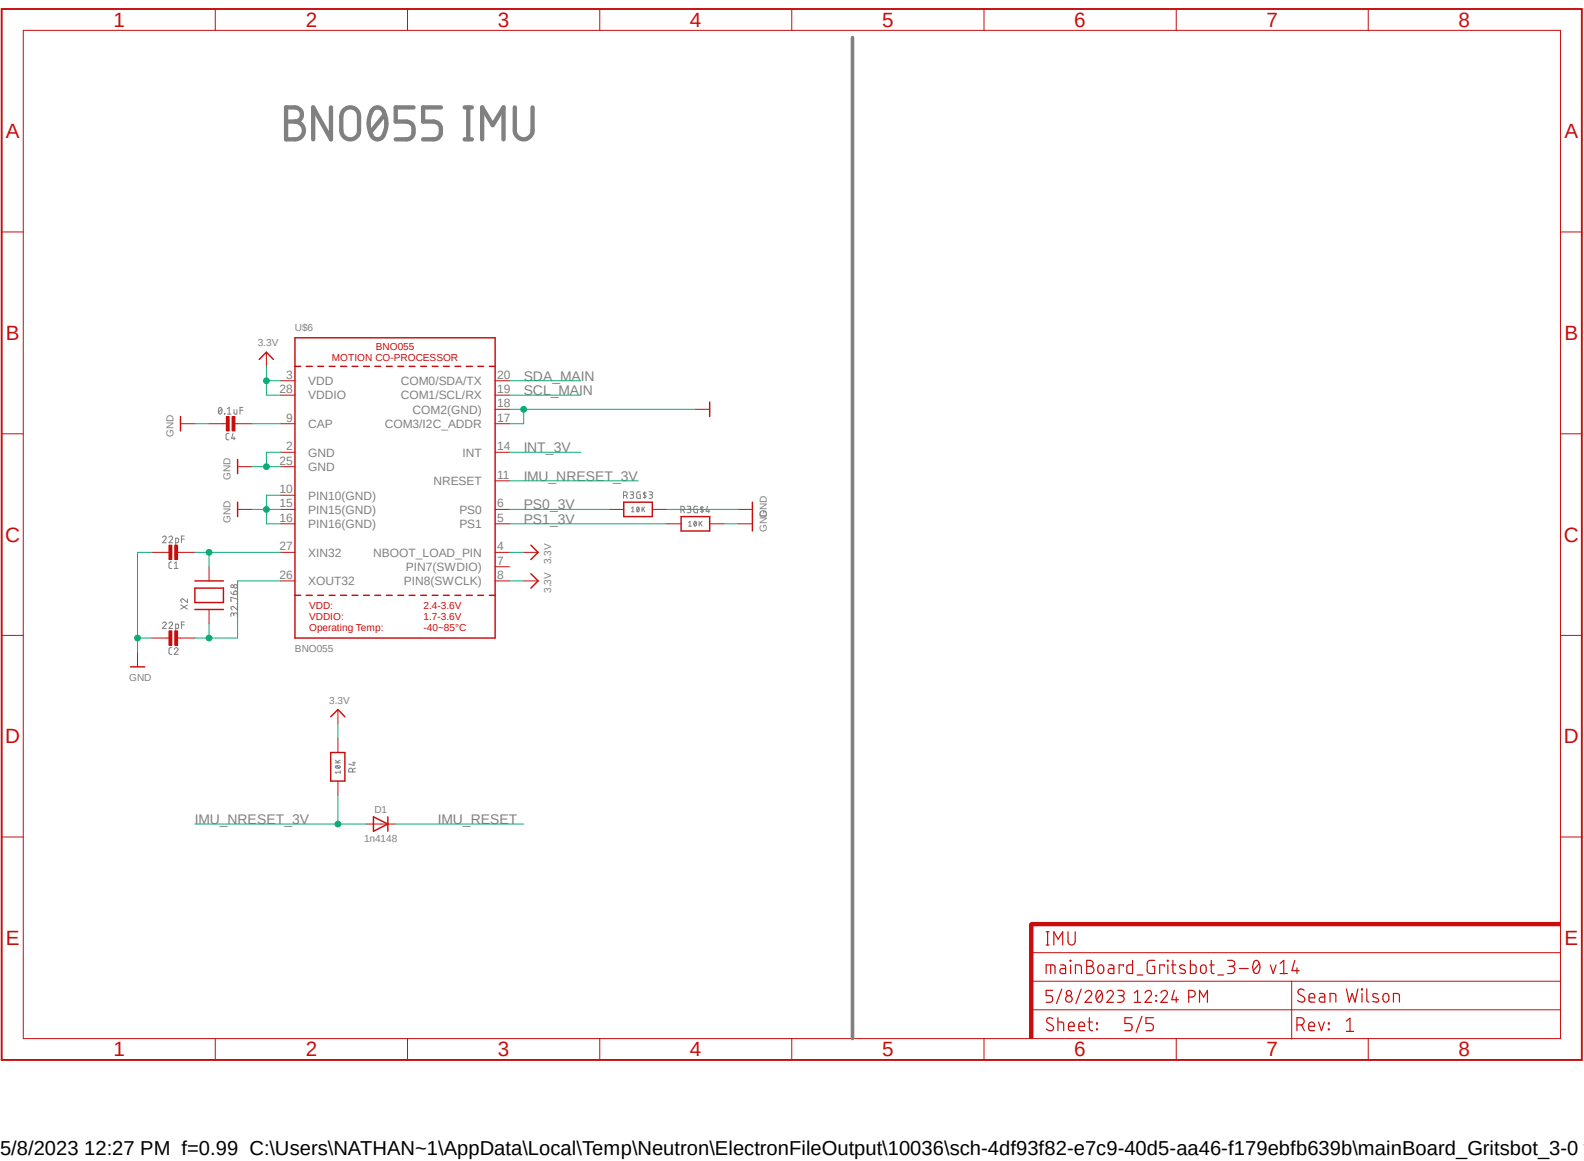
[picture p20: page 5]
BNO055 GND; GND GND GND; GND; U$6GND 2; VDD 3; NBOOT_LOAD_PIN; 6 CAP 9; PIN10(GND) 10; NRESET; INT; 14 PIN15(GND) 15; PIN16(GND) 16; COM3/I2C_ADDR; 17 COM2(GND); 18 COM1/SCL/RX; 19 COM0/SDA/TX; 20 GND 25; XOUT32 26; XIN32 27; VDDIO 28; PIN7(SWDIO); 7 PIN8(SWCLK); SCL_MAIN; SDA_MAIN; IMU_NRESET_3V; INT_3V; IMU_RESET; 8 BNO055 MOTION CO-PROCESSOR; VDD: VDDIO: Operating Temp:

5/8/2023 12:27 PM f=0.99 C:\Users\NATHAN~1\AppData\Local\Temp\Neutron\ElectronFileOutput\10036\sch-4df93f82-e7c9-40d5-aa46-f179ebfb639b\mainBoard_Gritsbot_3-0 v14.sch (Sheet: 5/5)

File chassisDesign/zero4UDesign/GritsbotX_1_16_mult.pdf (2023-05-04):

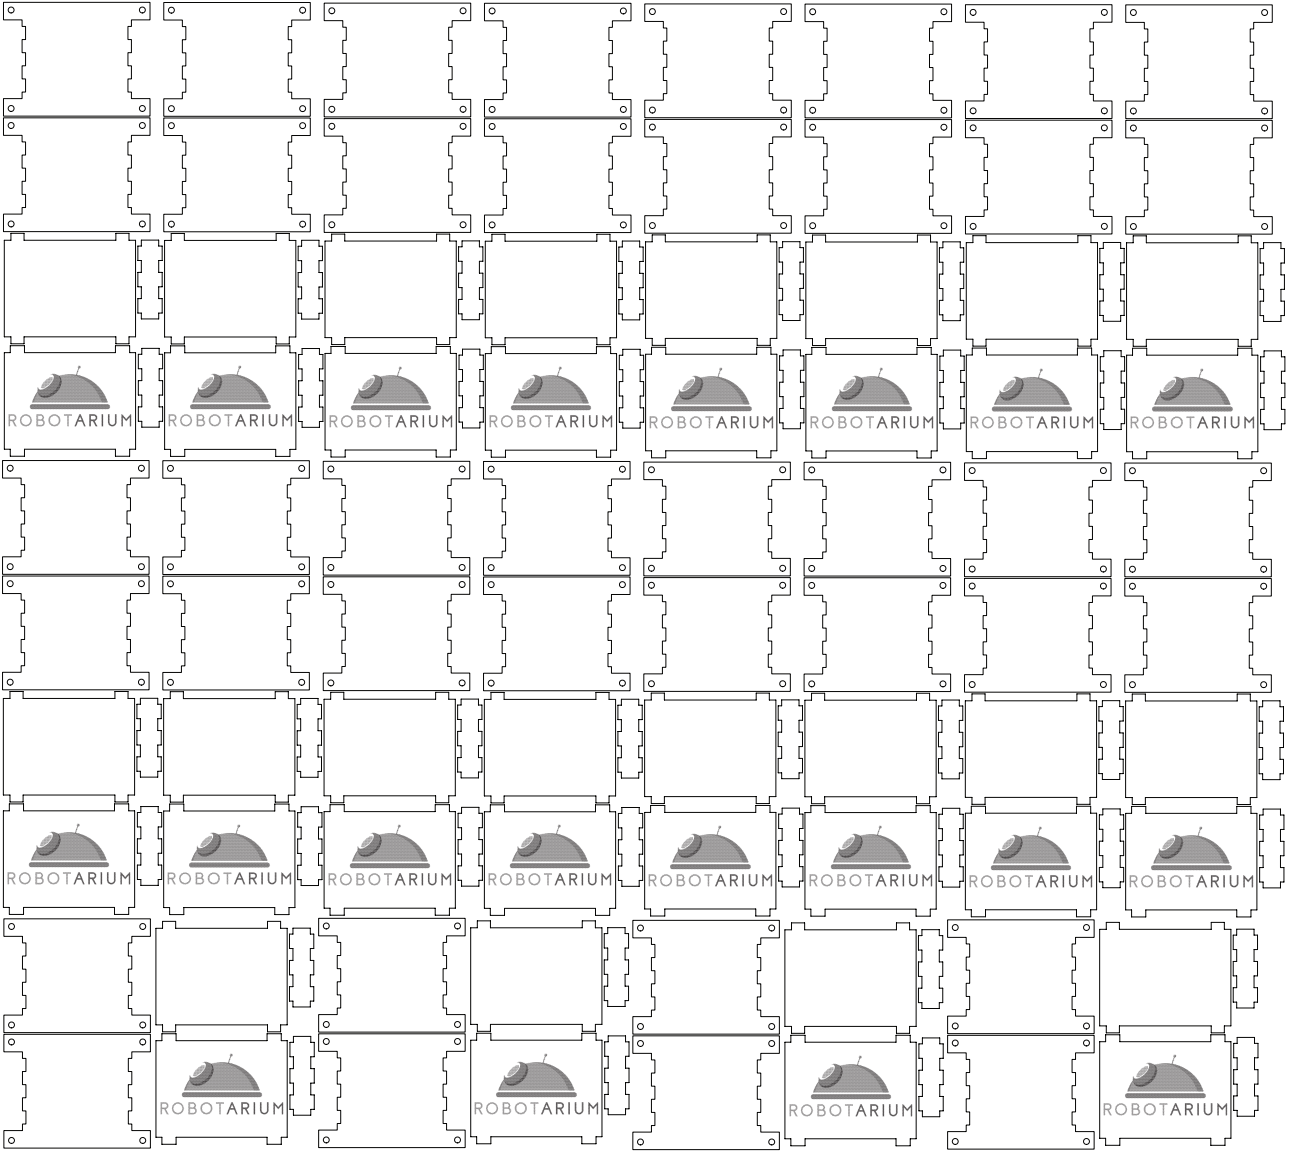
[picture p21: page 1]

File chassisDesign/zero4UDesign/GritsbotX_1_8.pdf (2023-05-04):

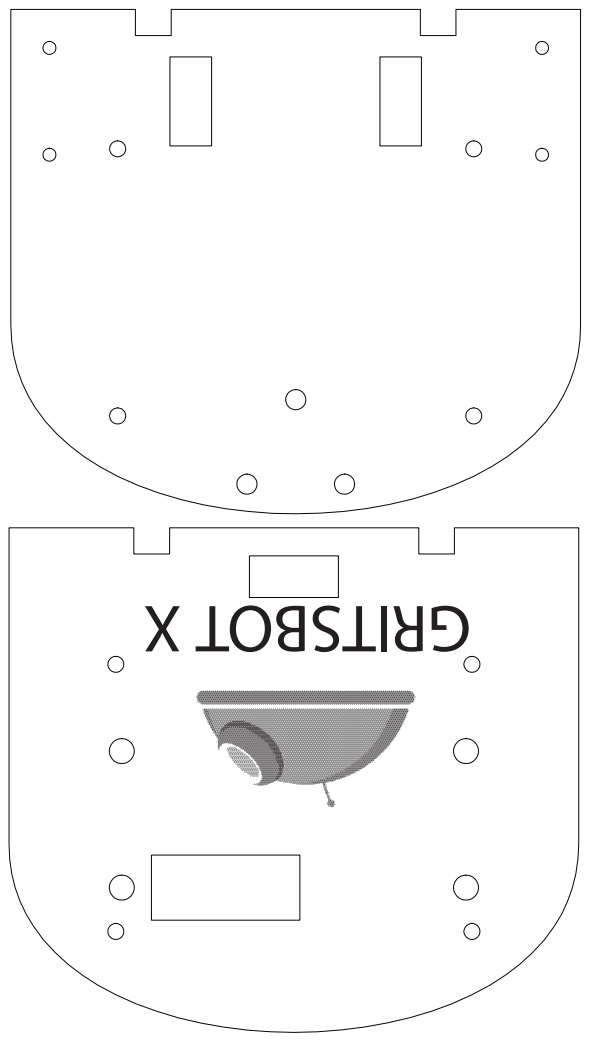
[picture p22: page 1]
GRITSBOT X

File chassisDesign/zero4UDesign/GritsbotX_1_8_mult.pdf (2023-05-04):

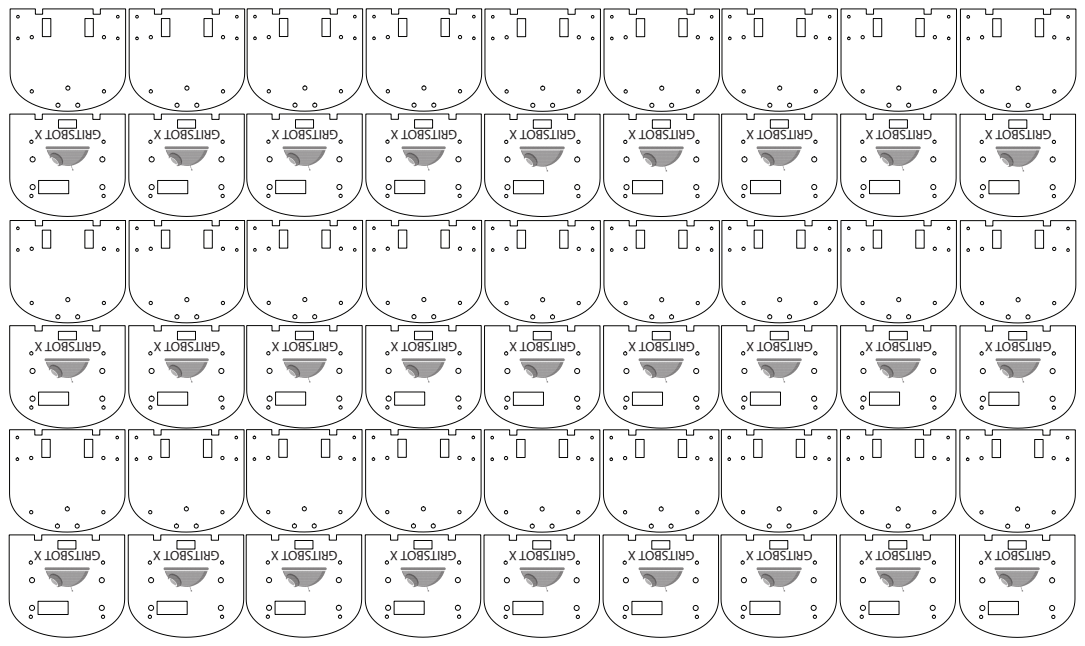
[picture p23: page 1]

GRITSBOT X GRITSBOT X GRITSBOT X GRITSBOT X GRITSBOT X GRITSBOT X GRITSBOT X GRITSBOT X GRITSBOT X

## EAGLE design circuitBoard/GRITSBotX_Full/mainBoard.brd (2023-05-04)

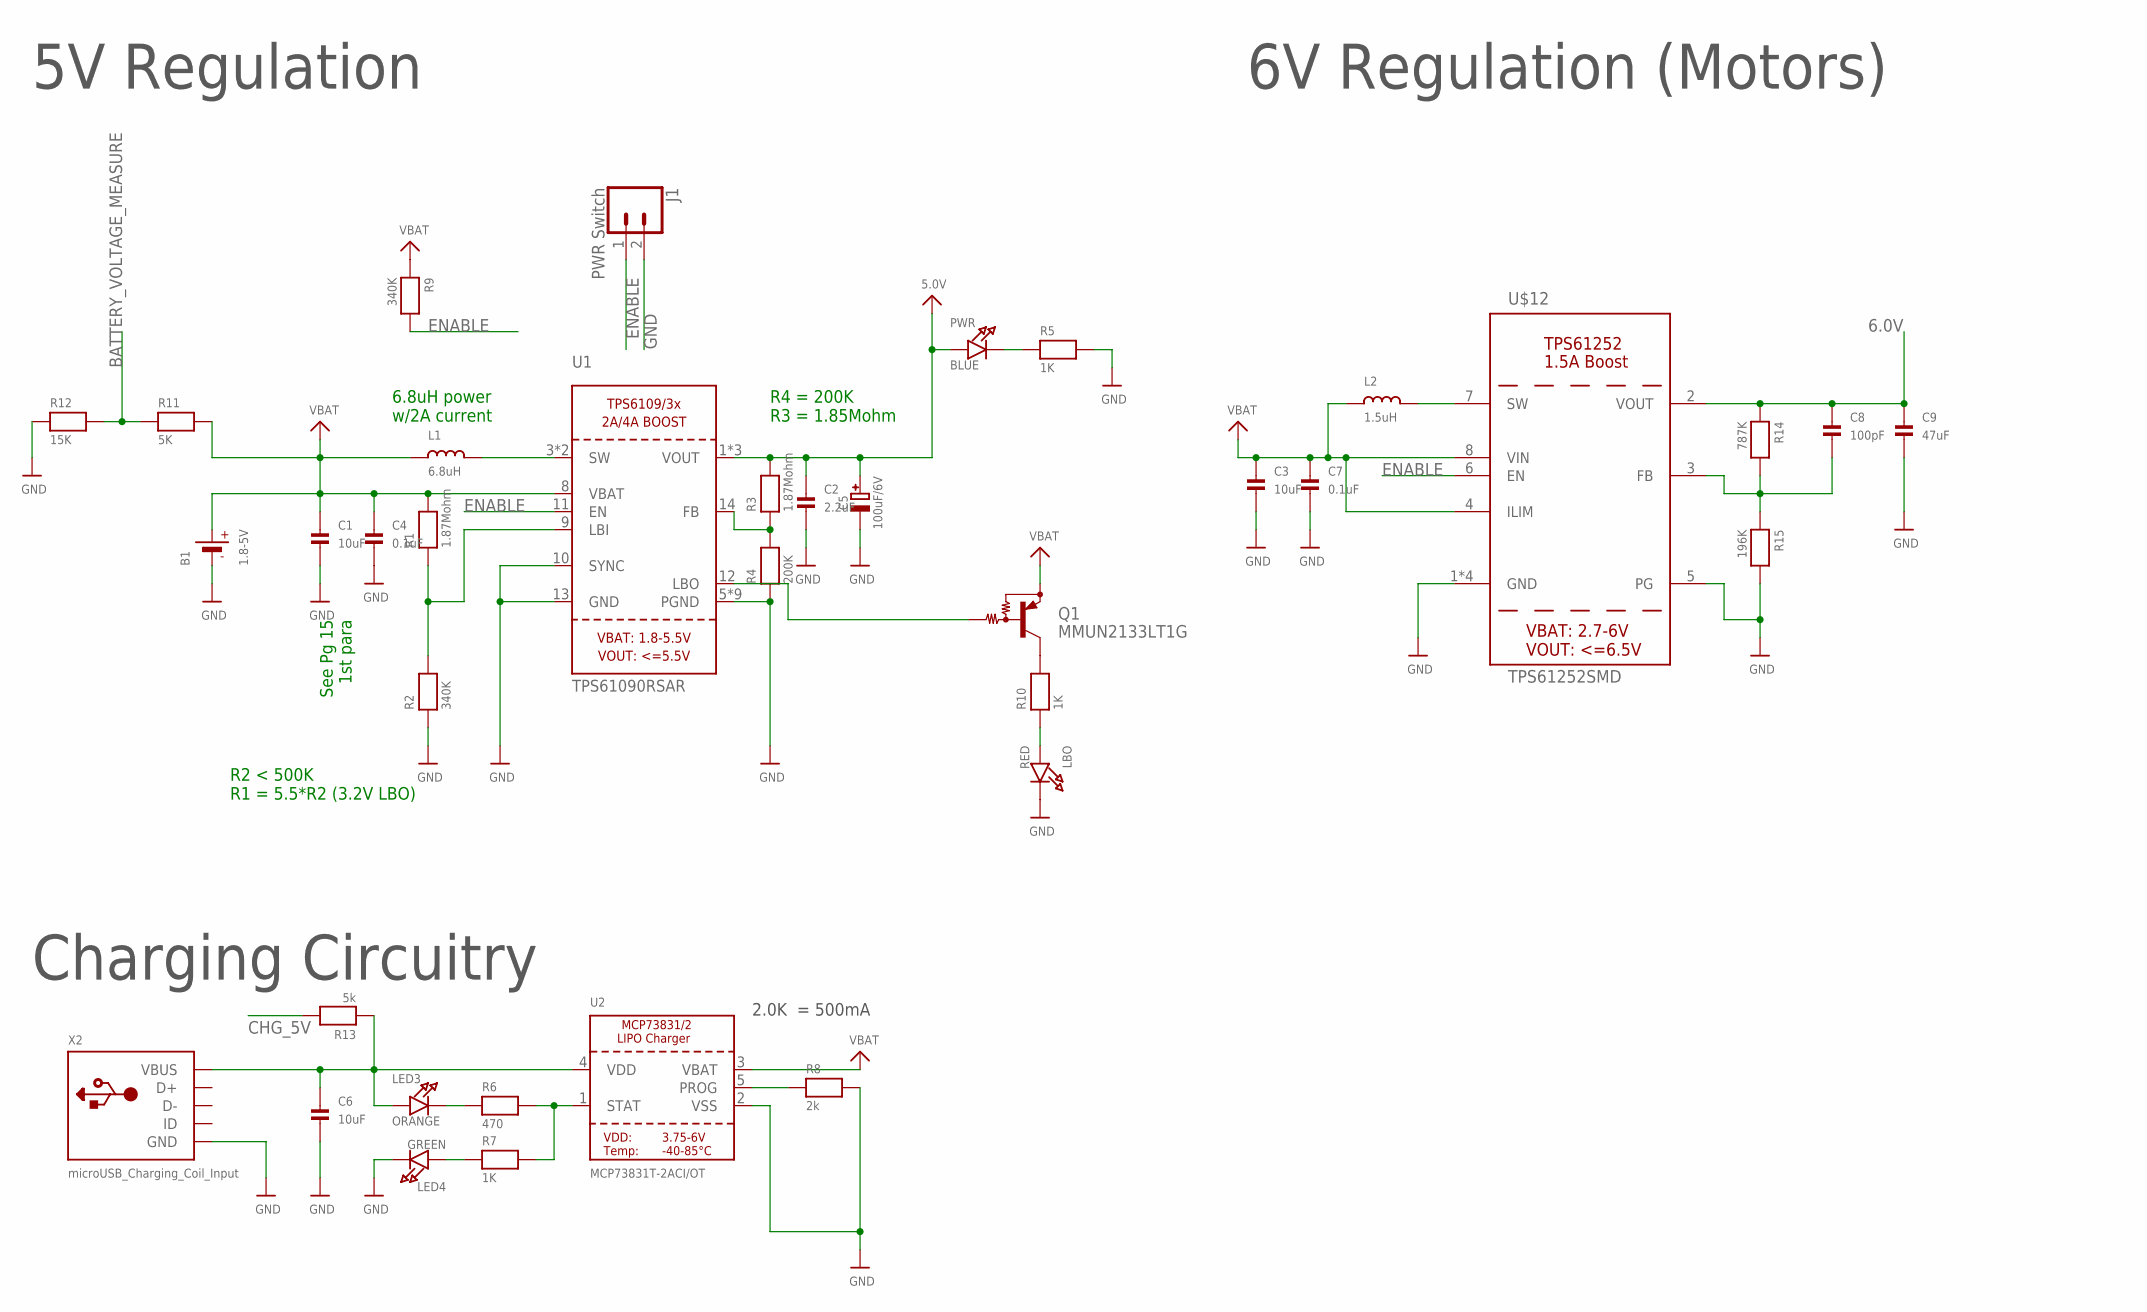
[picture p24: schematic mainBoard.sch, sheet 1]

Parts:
B1: 1.8-5V; JSTPH2
C1, C3, C6: 10uF; 0603
C2: 2.2uF; 0603
C4, C7: 0.1uF; 0805
C5: 100uF/6V; EIA3528-21/B-R
C8: 100pF; 0603
C9: 47uF; 1206
J1: PWR Switch; 1X02
L1: 6.8uH; VISHAY_IHLP2525CZER6R8M01
L2: 1.5uH; MURATA_DFE252012P-1R5M=P2
LBO: RED; CHIPLED_0805_NOOUTLINE
LED3: ORANGE; CHIPLED_0805_NOOUTLINE
LED4: GREEN; CHIPLED_0805_NOOUTLINE
PWR: BLUE; CHIPLED_0805_NOOUTLINE
Q1: MMUN2133LT1G; SC59-BEC
R1, R3: 1.87Mohm; 0805
R2, R9: 340K; 0805
R4: 200K; 0805
R5, R7, R10: 1K; 0805
R6: 470; 0805
R8: 2k; 0805
R11: 5K; 0805
R12: 15K; 0805
R13: 5k; 0805
R14: 787K; 0805
R15: 196K; 0805
U1: TPS61090RSAR; PVQFN-16
U2: MCP73831T-2ACI/OT; SOT23-5
U$12: TPS61252SMD; TPS61252
X2: microUSB_Charging_Coil_Input; 4UCONN_20329

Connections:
5.0V: C2.1, C5.+, PWR.A, R3.2, U1.1 (VOUT), U1.15 (VOUT), U1.16 (VOUT); also elsewhere on the board
6.0V: C8.1, C9.1, R14.1, U$12.2 (VOUT); also elsewhere on the board
BATTERY_VOLTAGE_MEASURE: R11.1, R12.2; also elsewhere on the board
CHARGING_BOOL_5V: C6.1, LED3.A, R13.1, U2.4 (VDD), X2.VBUS
CHG_5V: R13.2; also elsewhere on the board
ENABLE: J1.1, R9.2, U1.11 (EN), U$12.6 (EN)
GND: B1.1 (-), C1.2, C2.2, C3.2, C4.2, C5.-, C6.2, C7.2, C9.2, J1.2, LBO.C, LED4.C, R2.1, R4.1, R5.2, R8.2, R12.1, R15.2, U1.5 (PGND), U1.6 (PGND), U1.7 (PGND), U1.10 (SYNC), U1.13 (GND), U1.P$18 (PGND), U1.P$19 (PGND), U1.P$20 (PGND), U1.P$21 (PGND), U1.P$22 (PGND), U1.THERMAL (PGND), U2.2 (VSS), U$12.1 (GND), U$12.5 (PG), U$12.P$2_GND (GND), U$12.P$3_GND (GND), U$12.THERMAL_GND (GND), X2.BASE@1 (GND), X2.BASE@2 (GND), X2.GND, X2.SPRT@1 (GND), X2.SPRT@2 (GND), X2.SPRT@3 (GND), X2.SPRT@4 (GND); also elsewhere on the board
LBO: Q1.B, U1.12 (LBO)
unnamed: L1.P$2 (2), U1.3 (SW), U1.4 (SW)
unnamed: LBO.A, R10.1
unnamed: R1.1, R2.2, U1.9 (LBI)
unnamed: PWR.C, R5.1
unnamed: R3.1, R4.2, U1.14 (FB)
unnamed: LED3.C, R6.1
unnamed: R6.2, R7.2, U2.1 (STAT)
unnamed: R8.1, U2.5 (PROG)
unnamed: LED4.A, R7.1
unnamed: Q1.C, R10.2
unnamed: L2.P$2 (2), U$12.7 (SW)
unnamed: C8.2, R14.2, R15.1, U$12.3 (FB)
VBAT: B1.2 (+), C1.1, C3.1, C4.1, C7.1, L1.P$1 (1), L2.P$1 (1), Q1.E, R1.2, R9.1, R11.2, U1.8 (VBAT), U2.3 (VBAT), U$12.4 (ILIM), U$12.8 (VIN)

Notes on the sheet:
See Pg 15 1st para
6.8uH power w/2A current
R2 < 500K R1 = 5.5*R2 (3.2V LBO)
R4 = 200K R3 = 1.85Mohm
2.0K = 500mA
Charging Circuitry
5V Regulation
6V Regulation (Motors)

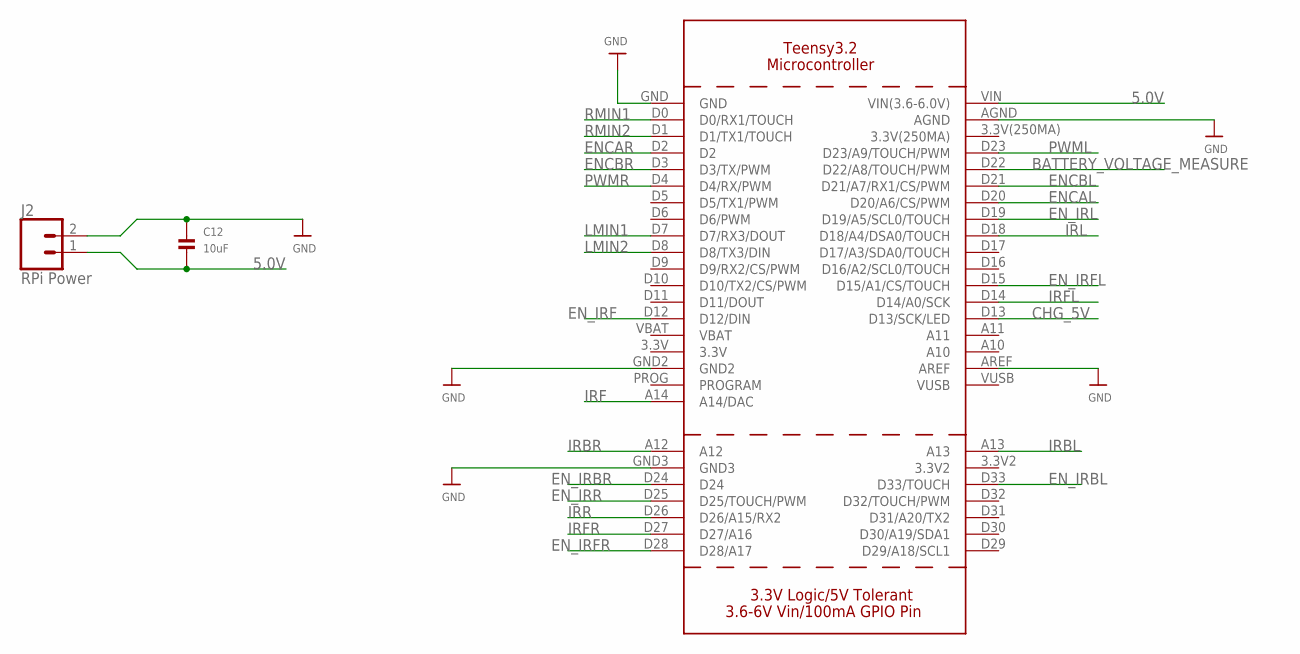
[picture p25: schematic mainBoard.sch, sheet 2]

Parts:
C12: 10uF; 0603
J2: RPi Power; 1X02
U$28: TEENSY3_2

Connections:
5.0V: C12.2, J2.1, U$28.VIN (VIN(3.6-6.0V)); also elsewhere on the board
BATTERY_VOLTAGE_MEASURE: U$28.D22 (D22/A8/TOUCH/PWM); also elsewhere on the board
CHG_5V: U$28.D13 (D13/SCK/LED); also elsewhere on the board
ENCAL: U$28.D20 (D20/A6/CS/PWM); also elsewhere on the board
ENCAR: U$28.D2; also elsewhere on the board
ENCBL: U$28.D21 (D21/A7/RX1/CS/PWM); also elsewhere on the board
ENCBR: U$28.D3 (D3/TX/PWM); also elsewhere on the board
EN_IRBL: U$28.D33 (D33/TOUCH); also elsewhere on the board
EN_IRBR: U$28.D24; also elsewhere on the board
EN_IRF: U$28.D12 (D12/DIN); also elsewhere on the board
EN_IRFL: U$28.D15 (D15/A1/CS/TOUCH); also elsewhere on the board
EN_IRFR: U$28.D28 (D28/A17); also elsewhere on the board
EN_IRL: U$28.D19 (D19/A5/SCL0/TOUCH); also elsewhere on the board
EN_IRR: U$28.D25 (D25/TOUCH/PWM); also elsewhere on the board
GND: C12.1, J2.2, U$28.AGND, U$28.AREF, U$28.GND, U$28.GND2, U$28.GND3; also elsewhere on the board
IRBL: U$28.A13; also elsewhere on the board
IRBR: U$28.A12; also elsewhere on the board
IRF: U$28.A14 (A14/DAC); also elsewhere on the board
IRFL: U$28.D14 (D14/A0/SCK); also elsewhere on the board
IRFR: U$28.D27 (D27/A16); also elsewhere on the board
IRL: U$28.D18 (D18/A4/DSA0/TOUCH); also elsewhere on the board
IRR: U$28.D26 (D26/A15/RX2); also elsewhere on the board
LMIN1: U$28.D7 (D7/RX3/DOUT); also elsewhere on the board
LMIN2: U$28.D8 (D8/TX3/DIN); also elsewhere on the board
PWML: U$28.D23 (D23/A9/TOUCH/PWM); also elsewhere on the board
PWMR: U$28.D4 (D4/RX/PWM); also elsewhere on the board
RMIN1: U$28.D0 (D0/RX1/TOUCH); also elsewhere on the board
RMIN2: U$28.D1 (D1/TX1/TOUCH); also elsewhere on the board

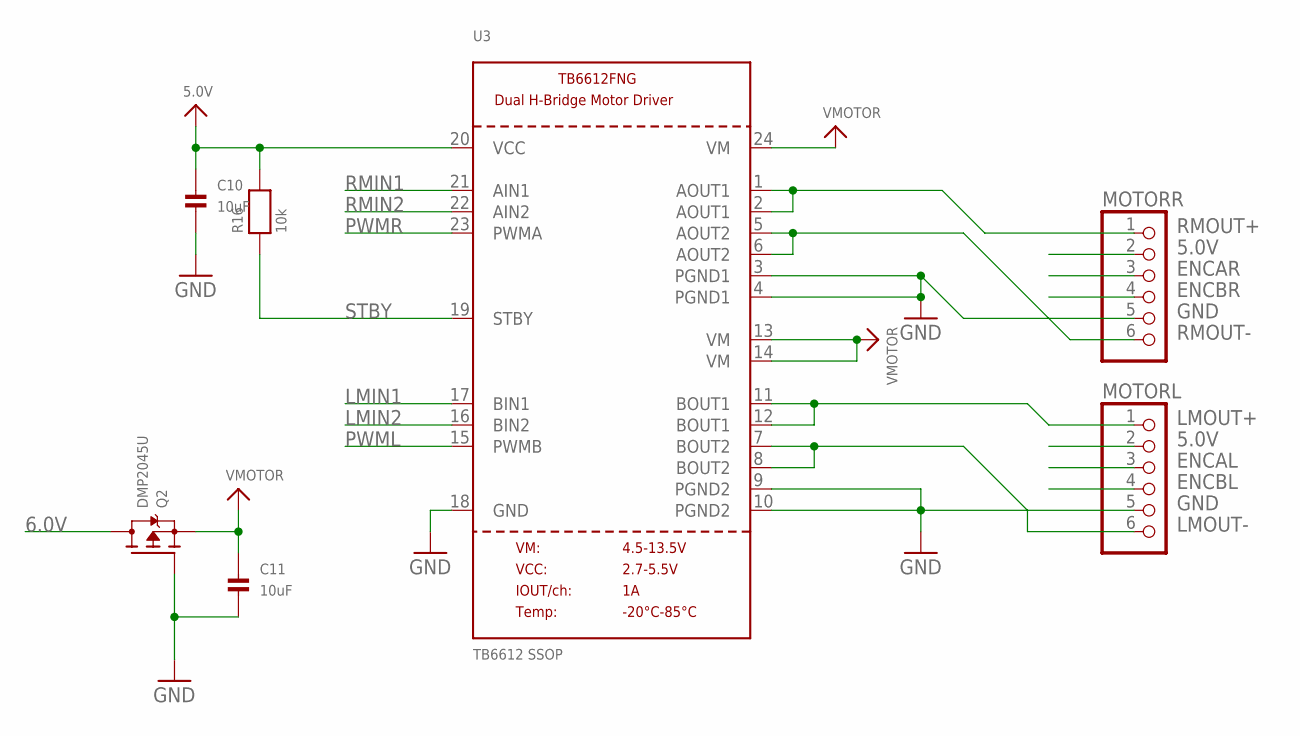
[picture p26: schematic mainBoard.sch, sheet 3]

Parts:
C10, C11: 10uF; 0603
MOTORL: PINHD-1X6CB; 1X06-CLEANBIG
MOTORR: PINHD-1X6CB; 1X06-CLEANBIG
Q2: DMP2045U; SOT23-WIDE
R16: 10k; 0805
U3: TB6612 SSOP; SSOP24

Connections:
5.0V: C10.1, MOTORL.2, MOTORR.2, R16.2, U3.20 (VCC); also elsewhere on the board
6.0V: Q2.3 (D); also elsewhere on the board
ENCAL: MOTORL.3; also elsewhere on the board
ENCAR: MOTORR.3; also elsewhere on the board
ENCBL: MOTORL.4; also elsewhere on the board
ENCBR: MOTORR.4; also elsewhere on the board
GND: C10.2, C11.2, MOTORL.5, MOTORR.5, Q2.1 (G), U3.3 (PGND1), U3.4 (PGND1), U3.9 (PGND2), U3.10 (PGND2), U3.18 (GND); also elsewhere on the board
LMIN1: U3.17 (BIN1); also elsewhere on the board
LMIN2: U3.16 (BIN2); also elsewhere on the board
LMOUT+: MOTORL.1, U3.11 (BOUT1), U3.12 (BOUT1)
LMOUT-: MOTORL.6, U3.7 (BOUT2), U3.8 (BOUT2)
PWML: U3.15 (PWMB); also elsewhere on the board
PWMR: U3.23 (PWMA); also elsewhere on the board
RMIN1: U3.21 (AIN1); also elsewhere on the board
RMIN2: U3.22 (AIN2); also elsewhere on the board
RMOUT+: MOTORR.1, U3.1 (AOUT1), U3.2 (AOUT1)
RMOUT-: MOTORR.6, U3.5 (AOUT2), U3.6 (AOUT2)
STBY: R16.1, U3.19 (STBY)
VMOTOR: C11.1, Q2.2 (S), U3.13 (VM), U3.14 (VM), U3.24 (VM)

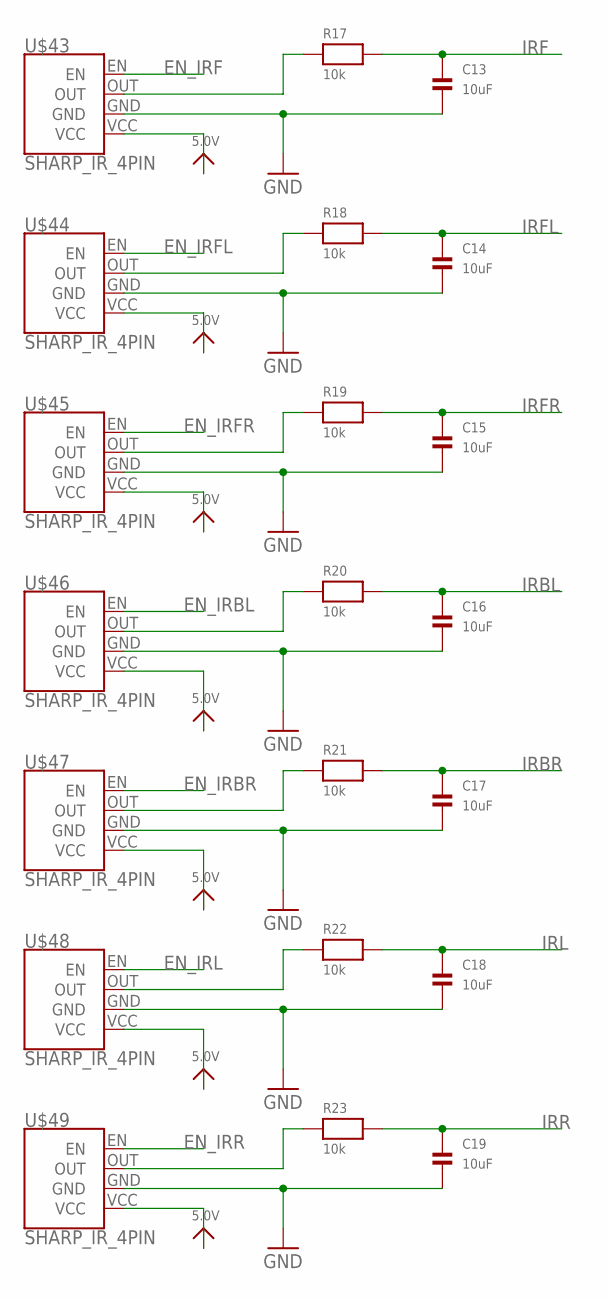
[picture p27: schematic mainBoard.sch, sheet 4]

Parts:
C13, C14, C15, C16, C17, C18, C19: 10uF; 0603
R17, R18, R19, R20, R21, R22, R23: 10k; 0805
U$43, U$44, U$45, U$46, U$47, U$48, U$49: SHARP_IR_4PIN

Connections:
5.0V: U$43.VCC, U$44.VCC, U$45.VCC, U$46.VCC, U$47.VCC, U$48.VCC, U$49.VCC; also elsewhere on the board
EN_IRBL: U$46.EN; also elsewhere on the board
EN_IRBR: U$47.EN; also elsewhere on the board
EN_IRF: U$43.EN; also elsewhere on the board
EN_IRFL: U$44.EN; also elsewhere on the board
EN_IRFR: U$45.EN; also elsewhere on the board
EN_IRL: U$48.EN; also elsewhere on the board
EN_IRR: U$49.EN; also elsewhere on the board
GND: C13.2, C14.2, C15.2, C16.2, C17.2, C18.2, C19.2, U$43.GND, U$44.GND, U$45.GND, U$46.GND, U$47.GND, U$48.GND, U$49.GND; also elsewhere on the board
IRBL: C16.1, R20.2; also elsewhere on the board
IRBR: C17.1, R21.2; also elsewhere on the board
IRF: C13.1, R17.2; also elsewhere on the board
IRFL: C14.1, R18.2; also elsewhere on the board
IRFR: C15.1, R19.2; also elsewhere on the board
IRL: C18.1, R22.2; also elsewhere on the board
IRR: C19.1, R23.2; also elsewhere on the board
unnamed: R23.1, U$49.OUT
unnamed: R22.1, U$48.OUT
unnamed: R21.1, U$47.OUT
unnamed: R20.1, U$46.OUT
unnamed: R19.1, U$45.OUT
unnamed: R18.1, U$44.OUT
unnamed: R17.1, U$43.OUT

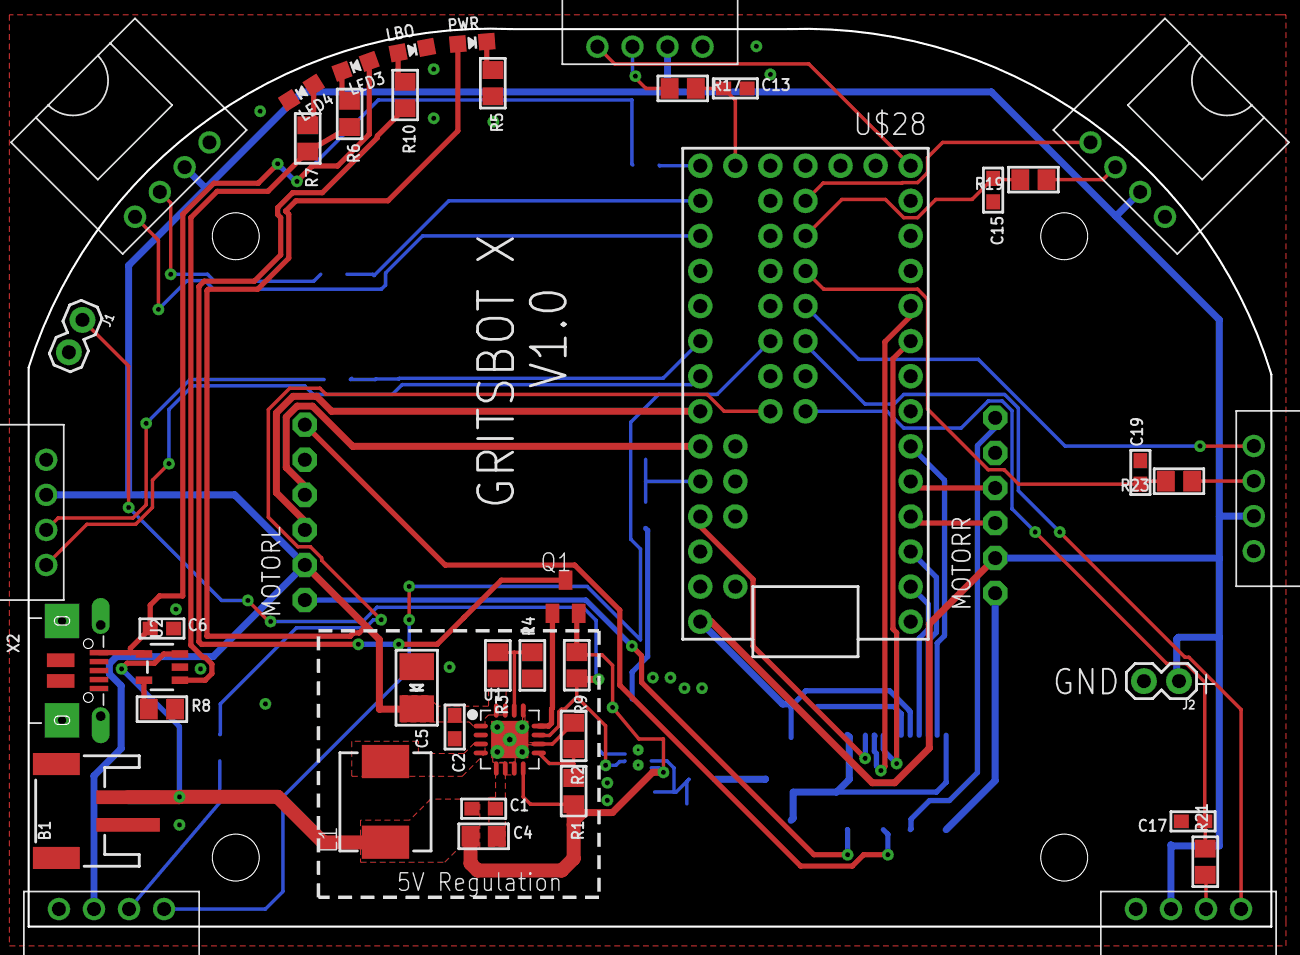
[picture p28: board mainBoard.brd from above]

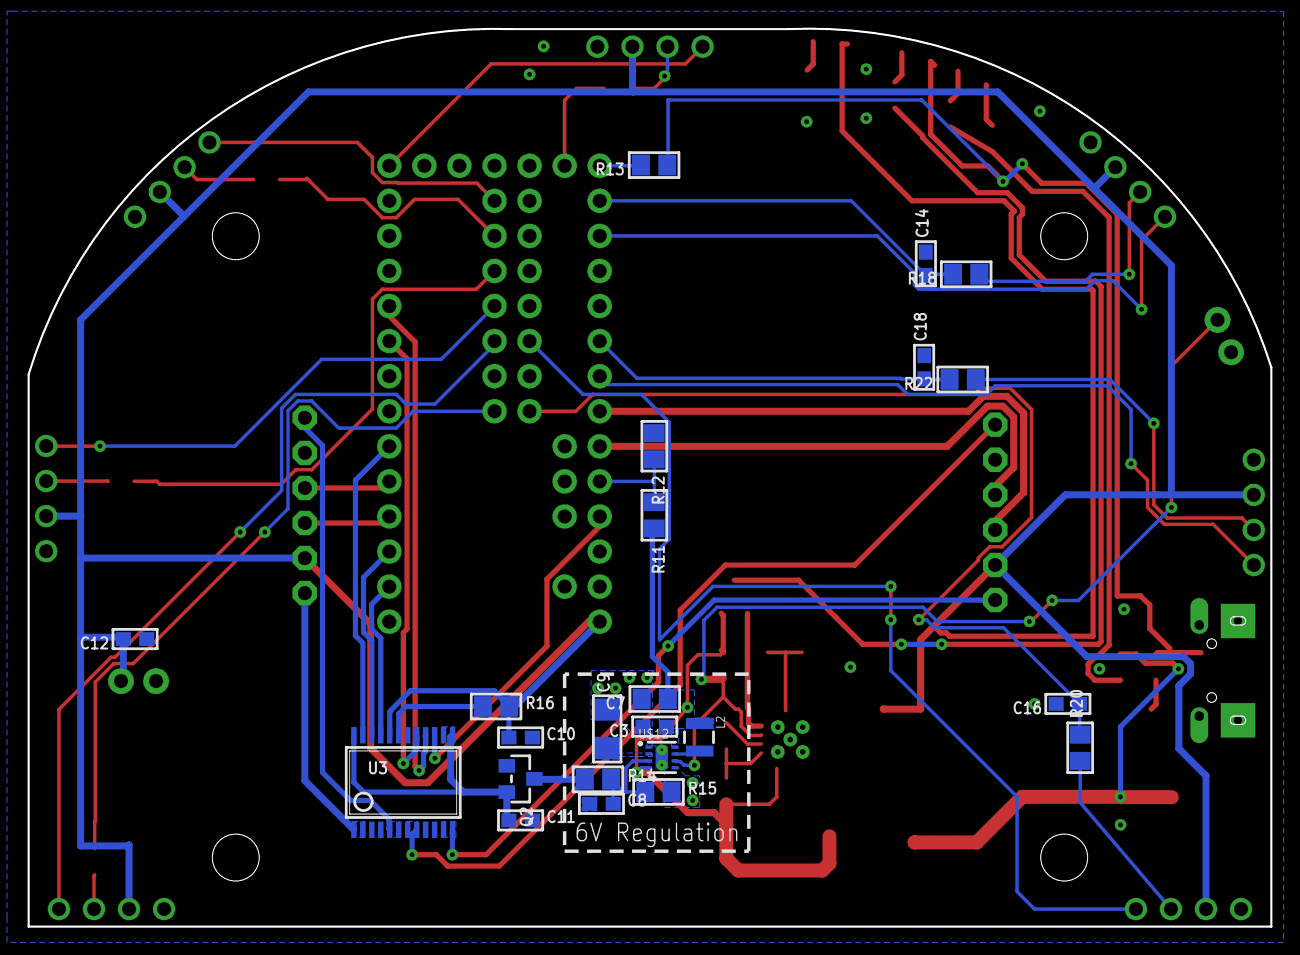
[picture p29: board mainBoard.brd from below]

Board: 2 copper layers, 90.0 x 65.0 mm, 72 parts (23 on the bottom side), 58 nets.

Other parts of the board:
U$1, U$2, U$3, U$4: M3_SCREW

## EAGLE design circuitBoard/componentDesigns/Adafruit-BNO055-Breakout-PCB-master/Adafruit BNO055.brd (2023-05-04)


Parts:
C1, C2: 22pF; 0805-NO
C3: 0.1uF; 0805-NO
C4: 0.1uF; 0805_10MGAP
C5: 10uF; 0805-NO
C6: 10uF; 0805_10MGAP
D1: 1n4148; SOD-323
FID1, FID2: FIDUCIAL""; FIDUCIAL_1MM
JP1: HEADER-1X676MIL; 1X06_ROUND_76
JP2: HEADER-1X476MIL; 1X04_ROUND_76
Q1, Q2: BSS138; SOT23-WIDE
R3, R4, R5, R6, R7, R10: 10K; 0805-NO
R8, R9: 10K; _0805MP
U1: MIC5225-3.3; SOT23-5
U$2: BNO055
U$29, U$30, U$31, U$32: MOUNTINGHOLE2.5_THICK; MOUNTINGHOLE_2.5_PLATED_THICK
Y1: 32.768kHz; CRYSTAL_8X3.8

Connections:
3.3V: C4.2, C6.1, JP1.2, Q1.1 (G), Q2.1 (G), R6.2, R7.2, R10.2, U1.5 (OUT), U$2.3 (VDD), U$2.4 (NBOOT_LOAD_PIN), U$2.28 (VDDIO)
5.0V: C5.1, JP1.1, R8.2, R9.2, U1.1 (IN), U1.3 (EN)
GND: C1.1, C2.1, C3.1, C4.1, C5.2, C6.2, JP1.3, R3.2, R4.2, R5.2, U1.2 (GND), U$2.2 (GND), U$2.10 (PIN10(GND)), U$2.15 (PIN15(GND)), U$2.16 (PIN16(GND)), U$2.18 (COM2(GND)), U$2.25 (GND)
I2CADDR_3V: JP2.4, R5.1, U$2.17 (COM3/I2C_ADDR)
INT_3V: JP2.3, U$2.14 (INT)
unnamed: C1.2, U$2.27 (XIN32), Y1.P$4 (2)
unnamed: C2.2, U$2.26 (XOUT32), Y1.P$1 (1)
unnamed: C3.2, U$2.9 (CAP)
NRESET_3V: D1.A, R10.1, U$2.11 (NRESET)
PS0_3V: JP2.1, R3.1, U$2.6 (PS0)
PS1_3V: JP2.2, R4.1, U$2.5 (PS1)
RST_5V: D1.C, JP1.6
SCL_3V: Q2.2 (S), R7.1, U$2.19 (COM1/SCL/RX)
SCL_5V: JP1.5, Q2.3 (D), R9.1
SDA_3V: Q1.2 (S), R6.1, U$2.20 (COM0/SDA/TX)
SDA_5V: JP1.4, Q1.3 (D), R8.1



Board: 2 copper layers, 26.7 x 20.3 mm, 31 parts (2 on the bottom side), 16 nets.

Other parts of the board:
U$3: PCBFEAT-REV-040
U$28: ADAFRUIT_TEXT_20MM
U$33: ADAFRUIT_2.5MM

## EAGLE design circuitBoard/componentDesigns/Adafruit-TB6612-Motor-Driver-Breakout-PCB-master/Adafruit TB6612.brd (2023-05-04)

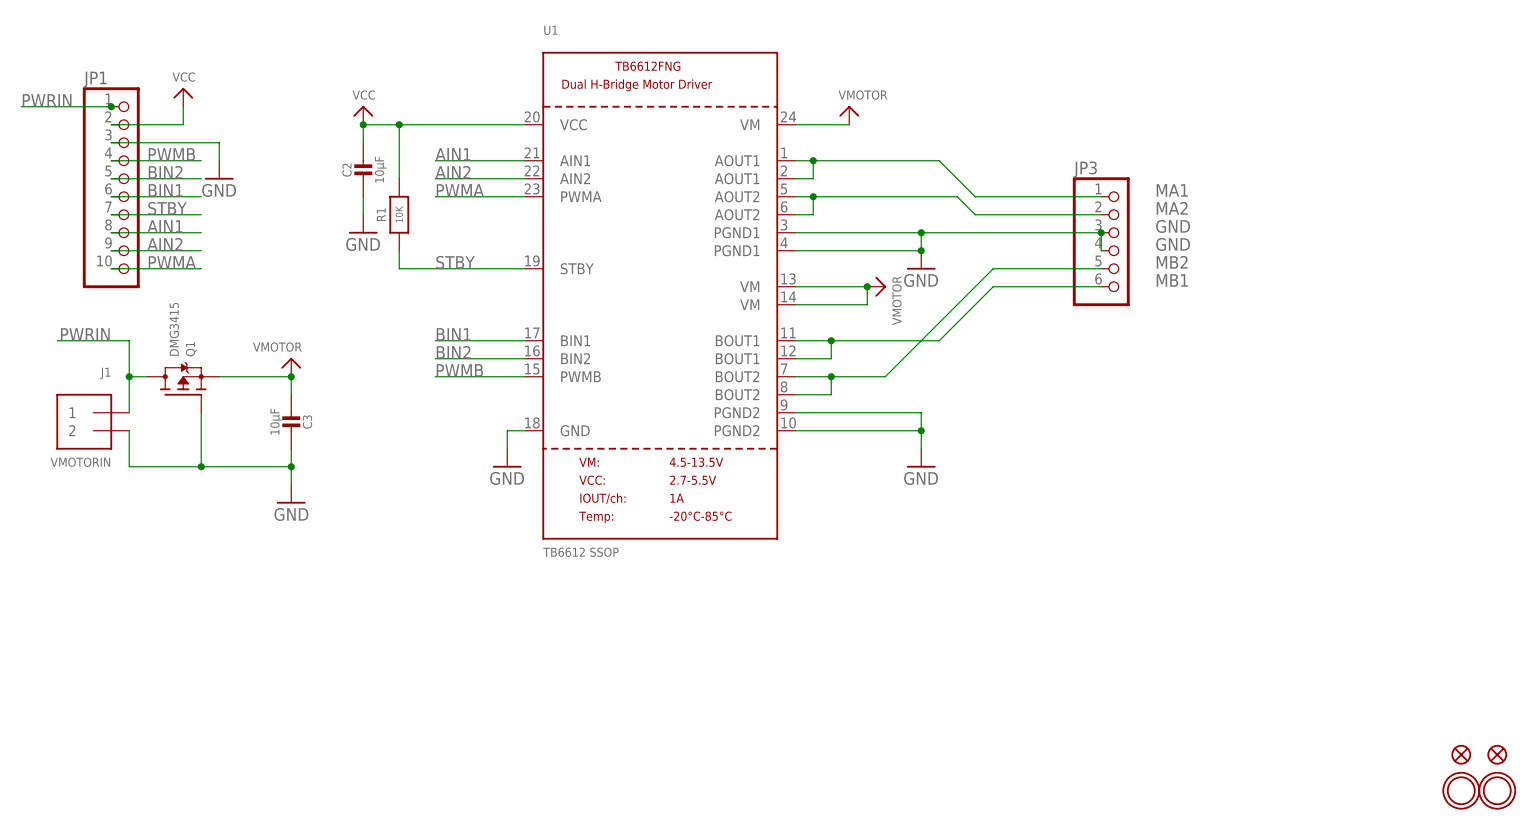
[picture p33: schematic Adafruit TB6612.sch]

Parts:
C2, C3: 10µF; 0805-NO
FID1, FID2: FIDUCIAL""; FIDUCIAL_1MM
J1: VMOTORIN; TERMBLOCK_1X2-3.5MM
JP1: HEADER-1X10THICKER; 1X10_ROUND_76
JP3: PINHD-1X6CB; 1X06-CLEANBIG
Q1: DMG3415; SOT23-WIDE
R1: 10K; 0805-NO
U1: TB6612 SSOP; SSOP24
U$13, U$14: MOUNTINGHOLE2.5; MOUNTINGHOLE_2.5_PLATED

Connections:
AIN1: JP1.8, U1.21 (AIN1)
AIN2: JP1.9, U1.22 (AIN2)
BIN1: JP1.6, U1.17 (BIN1)
BIN2: JP1.5, U1.16 (BIN2)
GND: C2.2, C3.2, J1.2, JP1.3, JP3.3, JP3.4, Q1.1 (G), U1.3 (PGND1), U1.4 (PGND1), U1.9 (PGND2), U1.10 (PGND2), U1.18 (GND)
MA1: JP3.1, U1.1 (AOUT1), U1.2 (AOUT1)
MA2: JP3.2, U1.5 (AOUT2), U1.6 (AOUT2)
MB1: JP3.6, U1.11 (BOUT1), U1.12 (BOUT1)
MB2: JP3.5, U1.7 (BOUT2), U1.8 (BOUT2)
PWMA: JP1.10, U1.23 (PWMA)
PWMB: JP1.4, U1.15 (PWMB)
PWRIN: J1.1, JP1.1, Q1.3 (D)
STBY: JP1.7, R1.1, U1.19 (STBY)
VCC: C2.1, JP1.2, R1.2, U1.20 (VCC)
VMOTOR: C3.1, Q1.2 (S), U1.13 (VM), U1.14 (VM), U1.24 (VM)

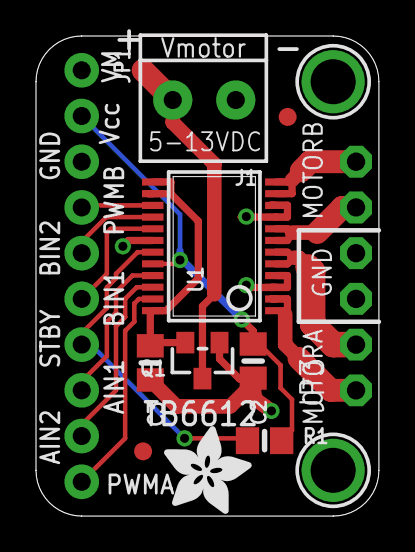
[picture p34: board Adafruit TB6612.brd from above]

Board: 2 copper layers, 19.1 x 26.7 mm, 14 parts (1 on the bottom side), 15 nets.

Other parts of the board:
U$11: ADAFRUIT_3.5MM
U$15: ADAFRUIT_5MM

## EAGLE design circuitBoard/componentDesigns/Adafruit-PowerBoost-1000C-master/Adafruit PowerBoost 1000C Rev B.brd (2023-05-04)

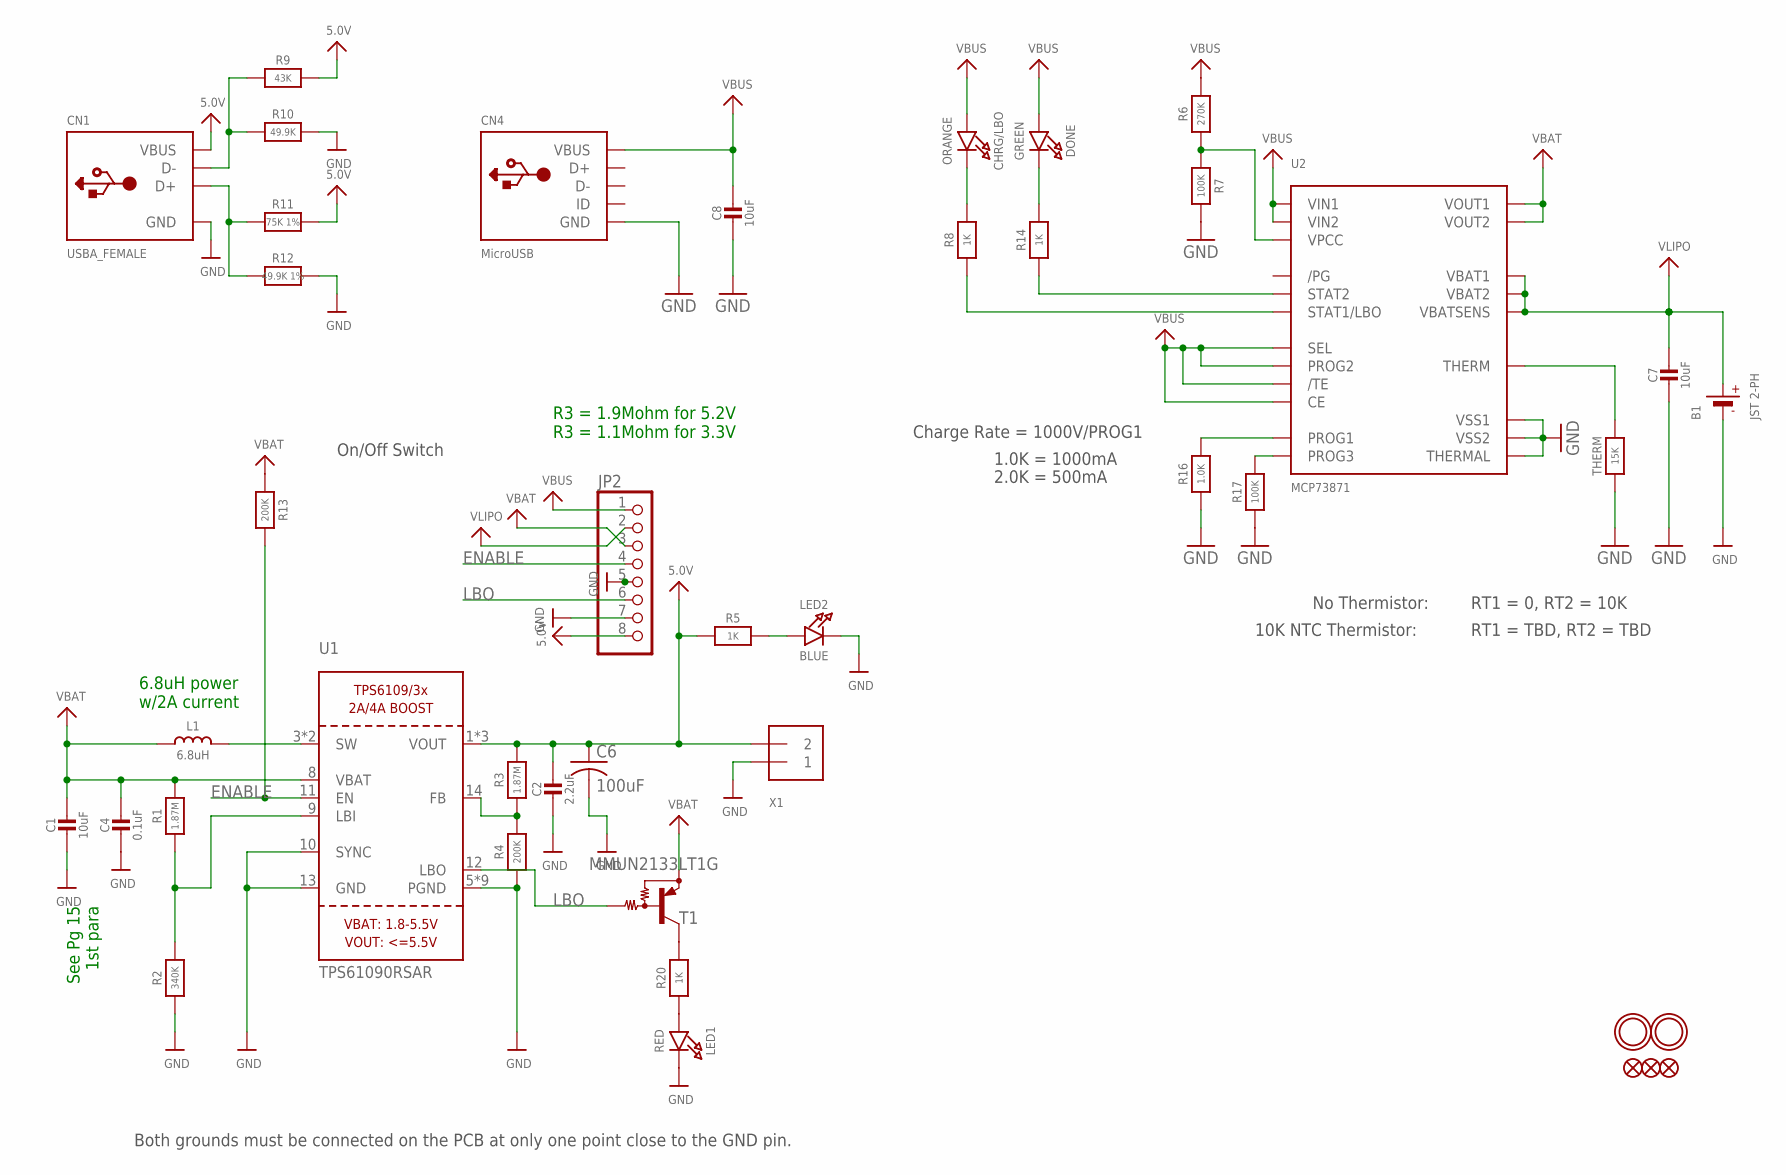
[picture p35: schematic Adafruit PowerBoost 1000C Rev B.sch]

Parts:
B1: JST 2-PH; JSTPH2
C1, C7, C8: 10uF; 0805-NO
C2: 2.2uF; 0805-NO
C4: 0.1uF; 0805_10MGAP
C6: 100uF; C1210
CHRG/LBO: ORANGE; CHIPLED_0805_NOOUTLINE
CN1: USBA_FEMALE; USB_HOST-PTH
CN4: MicroUSB; 4UCONN_20329
DONE: GREEN; CHIPLED_0805_NOOUTLINE
FID1, FID2, FID3: FIDUCIAL""; FIDUCIAL_1MM
JP2: HEADER-1X8ROUND; 1X08_ROUND
L1: 6.8uH; INDUCTOR_5X5MM_TDK_VLC5045
LED1: RED; CHIPLED_0805_NOOUTLINE
LED2: BLUE; CHIPLED_0805_NOOUTLINE
R1: 1.87M; _0805MP
R2: 340K; _0805MP
R3: 1.87M; 0805-NO
R4, R13: 200K; 0805-NO
R5, R8, R14, R20: 1K; 0805-NO
R6: 270K; 0805-NO
R7, R17: 100K; 0805-NO
R9: 43K; 0805-NO
R10: 49.9K; 0805-NO
R11: 75K 1%; 0805-NO
R12: 49.9K 1%; 0805-NO
R16: 1.0K; 0805-NO
T1: MMUN2133LT1G; SC59-BEC
THERM: 15K; 0805-NO
U1: TPS61090RSAR; PVQFN-16
U2: MCP73871; QFN20_4MM
U$10, U$11: MOUNTINGHOLE2.5; MOUNTINGHOLE_2.5_PLATED
X1: TERMBLOCK_1X2; TERMBLOCK_1X2-3.5MM

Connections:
5.0V: C2.1, C6.1, CN1.VBUS, JP2.8, R3.2, R5.1, R9.2, R11.2, U1.1 (VOUT), U1.15 (VOUT), U1.16 (VOUT), X1.2
D+: CN1.D+, R11.1, R12.1
D-: CN1.D-, R9.1, R10.1
ENABLE: JP2.4, R13.2, U1.11 (EN)
GND: B1.1 (-), C1.2, C2.2, C4.2, C6.2, C7.2, C8.2, CN1.GND, CN4.BASE@1 (GND), CN4.BASE@2 (GND), CN4.GND, CN4.SPRT@1 (GND), CN4.SPRT@2 (GND), CN4.SPRT@3 (GND), CN4.SPRT@4 (GND), JP2.5, JP2.7, LED1.C, LED2.C, R2.1, R4.1, R7.2, R10.2, R12.2, R16.1, R17.1, THERM.1, U1.5 (PGND), U1.6 (PGND), U1.7 (PGND), U1.10 (SYNC), U1.13 (GND), U1.P$18 (PGND), U1.P$19 (PGND), U1.P$20 (PGND), U1.P$21 (PGND), U1.P$22 (PGND), U1.THERMAL (PGND), U2.P$10 (VSS1), U2.P$11 (VSS2), U2.P$21 (THERMAL), X1.1
LBO: JP2.6, T1.B, U1.12 (LBO)
unnamed: L1.P$2 (2), U1.3 (SW), U1.4 (SW)
unnamed: LED1.A, R20.1
unnamed: R1.1, R2.2, U1.9 (LBI)
unnamed: LED2.A, R5.2
unnamed: R3.1, R4.2, U1.14 (FB)
unnamed: R20.2, T1.C
unnamed: R6.1, R7.1, U2.P$2 (VPCC)
unnamed: DONE.C, R14.2
unnamed: R14.1, U2.P$7 (STAT2)
unnamed: THERM.2, U2.P$5 (THERM)
unnamed: R8.1, U2.P$8 (STAT1/LBO)
unnamed: CHRG/LBO.C, R8.2
unnamed: R17.2, U2.P$12 (PROG3)
unnamed: R16.2, U2.P$13 (PROG1)
VBAT: C1.1, C4.1, JP2.3, L1.P$1 (1), R1.2, R13.1, T1.E, U1.8 (VBAT), U2.P$1 (VOUT1), U2.P$20 (VOUT2)
VBUS: C8.1, CHRG/LBO.A, CN4.VBUS, DONE.A, JP2.1, R6.2, U2.P$3 (SEL), U2.P$4 (PROG2), U2.P$9 (/TE), U2.P$17 (CE), U2.P$18 (VIN1), U2.P$19 (VIN2)
VLIPO: B1.2 (+), C7.1, JP2.2, U2.P$14 (VBAT1), U2.P$15 (VBAT2), U2.P$16 (VBATSENS)

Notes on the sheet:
Both grounds must be connected on the PCB at only one point close to the GND pin.
On/Off Switch
See Pg 15 1st para
6.8uH power w/2A current
R3 = 1.9Mohm for 5.2V R3 = 1.1Mohm for 3.3V
Charge Rate = 1000V/PROG1
1.0K = 1000mA
2.0K = 500mA
No Thermistor:
10K NTC Thermistor:
RT1 = 0, RT2 = 10K
RT1 = TBD, RT2 = TBD



Board: 2 copper layers, 36.1 x 22.9 mm, 47 parts (2 on the bottom side), 23 nets.

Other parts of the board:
U$12: PCBFEAT-REV-040
U$25: SYMBOL_PLUS
U$26: SYMBOL_MINUS
U$28: ADAFRUIT_5MM
U$45: ADAFRUIT_3.5MM

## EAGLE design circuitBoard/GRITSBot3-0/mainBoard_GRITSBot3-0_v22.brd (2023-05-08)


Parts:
B1: 1.8-5V; JSTPH2
C3: 10uF; 0603
C7: 0.1uF; 0805
C8: 100pF; 0603
C9: 47uF; 1206
C13, C17, C49: 10uF; 0805-NO
C14: 2.2uF; 0805-NO
C15: 0.1uF; 0805_10MGAP
C16: 100uF; C1210
C28: 1uF; 0603-NO
CHRG: ORANGE; CHIPLED_0805_NOOUTLINE
CN4: microUSB_Charging_Coil_Input; 4UCONN_20329
DONE: GREEN; CHIPLED_0805_NOOUTLINE
IC1: INA260; TSSOP16
JP1: JP1Q; JP1
L2: 1.5uH; MURATA_DFE252012P-1R5M=P2
L3: 6.8uH; INDUCTOR_5X5MM_TDK_VLC5045
LBO: RED; CHIPLED_0805_NOOUTLINE
PWR: BLUE; CHIPLED_0805_NOOUTLINE
R1, R25: 200K; 0805-NO
R11: 5K; 0805
R12: 15K; 0805
R13: 5k; 0805
R14: 787K; 0805
R15: 196K; 0805
R21, R22, R121, R122: 1K; 0805-NO
R24: 1.87M; 0805-NO
R26: 340K; _0805MP
R27: 1.87M; _0805MP
R119: 270K; 0805-NO
R120, R124: 100K; 0805-NO
R123: 1.0K; 0805-NO
S1: MHSS1105
T1: MMUN2133LT1G; SC59-BEC
THERM6: 15K; 0805-NO
U1: TEXAS_INSTRUMENTS_TPS61030PWPTEXAS_INSTRUMENTS_TP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; TEXAS_INSTRUMENTS_TPS61030PWP_0
U16: MCP73871; QFN20_4MM
U$12: TPS61252SMD; TPS61252

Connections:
3.3V: C28.1, IC1.10 (VS); also elsewhere on the board
5.0V: C14.1, C16.1, R22.1, R24.2, U1.13 (1_VOUT), U1.14 (2_VOUT), U1.15 (3_VOUT); also elsewhere on the board
6.0V: C8.1, C9.1, R14.1, U$12.2 (VOUT); also elsewhere on the board
ALERT: IC1.7 (ALERT)
CHG_5V: R13.2; also elsewhere on the board
ENABLE: R1.2, S1.2 (COM), U1.9 (EN), U$12.6 (EN)
GND: B1.1 (-), C3.2, C7.2, C9.2, C13.2, C14.2, C15.2, C16.2, C17.2, C28.2, C49.2, CN4.BASE@1 (GND), CN4.BASE@2 (GND), CN4.GND, CN4.SPRT@1 (GND), CN4.SPRT@2 (GND), CN4.SPRT@3 (GND), CN4.SPRT@4 (GND), IC1.4 (A1), IC1.5 (A0), IC1.6 (GND), IC1.11 (GND), IC1.13 (GND), LBO.C, PWR.C, R12.1, R15.2, R25.1, R26.1, R120.2, R123.1, R124.1, S1.3 (NO), THERM6.1, U1.3 (1_PGND), U1.4 (2_PGND), U1.5 (3_PGND), U1.8 (SYNC), U1.11 (GND), U1.16 (NC), U1.17 (PGND_PAD), U1.PAD_1 (PGND_PAD), U1.PAD_2 (PGND_PAD), U1.PAD_3 (PGND_PAD), U1.PAD_4 (PGND_PAD), U1.PAD_5 (PGND_PAD), U1.PAD_6 (PGND_PAD), U16.P$10 (VSS1), U16.P$11 (VSS2), U16.P$21 (THERMAL), U$12.1 (GND), U$12.5 (PG), U$12.P$2_GND (GND), U$12.P$3_GND (GND), U$12.THERMAL_GND (GND); also elsewhere on the board
LBO: T1.B, U1.10 (LBO)
unnamed: R24.1, R25.2, U1.12 (FB)
unnamed: L2.P$2 (2), U$12.7 (SW)
unnamed: C8.2, R14.2, R15.1, U$12.3 (FB)
unnamed: L3.P$2 (2), U1.1 (1_SW), U1.2 (2_SW)
unnamed: R26.2, R27.1, U1.7 (LBI)
unnamed: LBO.A, R21.1
unnamed: R21.2, T1.C
unnamed: PWR.A, R22.2
unnamed: R119.1, R120.1, U16.P$2 (VPCC)
unnamed: R122.1, U16.P$7 (STAT2)
unnamed: R121.1, U16.P$8 (STAT1/LBO)
unnamed: R123.2, U16.P$13 (PROG1)
unnamed: THERM6.2, U16.P$5 (THERM)
unnamed: DONE.C, R122.2
unnamed: CHRG.C, R121.2
unnamed: R124.2, U16.P$12 (PROG3)
SCL_MAIN: IC1.9 (SCL); also elsewhere on the board
SDA_MAIN: IC1.8 (SDA); also elsewhere on the board
VBAT: C3.1, C7.1, C13.1, C15.1, IC1.14 (IN-), IC1.15 (IN-), IC1.16 (IN-), JP1.2, L2.P$1 (1), L3.P$1 (1), R1.1, R11.2, R27.2, T1.E, U1.6 (VBAT), U$12.4 (ILIM), U$12.8 (VIN)
VBAT_IN: IC1.1 (IN+), IC1.2 (IN+), IC1.3 (IN+), IC1.12 (VBUS), JP1.1, U16.P$1 (VOUT1), U16.P$20 (VOUT2)
VBAT_MEASURE: R11.1, R12.2; also elsewhere on the board
VBUS: C17.1, CHRG.A, CN4.VBUS, DONE.A, R13.1, R119.2, U16.P$3 (SEL), U16.P$4 (PROG2), U16.P$9 (/TE), U16.P$17 (CE), U16.P$18 (VIN1), U16.P$19 (VIN2)
VLIPO: B1.2 (+), C49.1, U16.P$14 (VBAT1), U16.P$15 (VBAT2), U16.P$16 (VBATSENS)

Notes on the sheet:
R2 < 500K R1 = 5.5*R2 (3.2V LBO)
Charging Circuitry
5V Regulation
6V Regulation (Motors)
Charge Rate = 1000V/PROG1
1.0K = 1000mA
2.0K = 500mA
No Thermistor:
10K NTC Thermistor:
RT1 = 0, RT2 = 10K
RT1 = TBD, RT2 = TBD
Both grounds must be connected on the PCB at only one point close to the GND pin.
On/Off Switch
See Pg 15 1st para
6.8uH power w/2A current
R3 = 1.9Mohm for 5.2V R3 = 1.1Mohm for 3.3V
Power Monitor


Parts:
C12: 10uF; 0603
J4: CONN_041X04_NO_SILK; 1X04_NO_SILK
R9: 10K; RESPACK_4X0603
U$57: TEENSY40

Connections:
3.3V: R9.1, R9.4 (1), U$57.3V3-1; also elsewhere on the board
5.0V: C12.2, J4.4, U$57.VIN; also elsewhere on the board
CHG_5V: U$57.13-SCK/CRX1/LED; also elsewhere on the board
ENCAL: U$57.20-A6/TX5/LRCLK1; also elsewhere on the board
ENCAR: U$57.2-OUT2; also elsewhere on the board
ENCBL: U$57.21-A7/RX5/BCLK1; also elsewhere on the board
ENCBR: U$57.3-LRCLK2; also elsewhere on the board
GND: C12.1, J4.3, U$57.GND1, U$57.GND2, U$57.GND3; also elsewhere on the board
I2CMUX_!RST: U$57.17-A3/TX4/SDA1; also elsewhere on the board
IMU_RESET: U$57.16-A2/RX4/SCL1; also elsewhere on the board
LMIN1: U$57.7-RX2/OUT1A (7-OUT1A/RX2); also elsewhere on the board
LMIN2: U$57.8-TX2/IN1 (8-IN1/TX2); also elsewhere on the board
PWML: U$57.23-A9/CRX1/CCLK1 (23-A9/CRX1/MCLK1); also elsewhere on the board
PWMR: U$57.4-BCLK2 (4-BCLK1); also elsewhere on the board
RMIN1: U$57.0-RX1 (0-RX1/CRX2); also elsewhere on the board
RMIN2: U$57.1-TX1 (1-TX1/CTX2); also elsewhere on the board
RPI_RX: J4.1, U$57.14-A0/TX3/S-PFI_OUT (14-A0/TX3/S-PDIF_IN)
RPI_TX: J4.2, U$57.15-A1/RX3/S-PDIF_IN (15-A1/RX3/SPDIF_IN)
SCL_MAIN: R9.8 (2), U$57.19-A5/SCL0; also elsewhere on the board
SDA_MAIN: R9.5 (2), U$57.18-A4/SDA0; also elsewhere on the board
VBAT_MEASURE: U$57.22-A8/CTX1; also elsewhere on the board


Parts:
C10, C11: 10uF; 0603
MOTORL: PINHD-1X6CB; 1X06-CLEANBIG
MOTORR: PINHD-1X6CB; 1X06-CLEANBIG
Q2: DMP2045U; SOT23-WIDE
R16: 10k; 0805
U3: TB6612 SSOP; SSOP24

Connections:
5.0V: C10.1, MOTORL.2, MOTORR.2, R16.2, U3.20 (VCC); also elsewhere on the board
6.0V: Q2.3 (D); also elsewhere on the board
ENCAL: MOTORL.3; also elsewhere on the board
ENCAR: MOTORR.3; also elsewhere on the board
ENCBL: MOTORL.4; also elsewhere on the board
ENCBR: MOTORR.4; also elsewhere on the board
GND: C10.2, C11.2, MOTORL.5, MOTORR.5, Q2.1 (G), U3.3 (PGND1), U3.4 (PGND1), U3.9 (PGND2), U3.10 (PGND2), U3.18 (GND); also elsewhere on the board
LMIN1: U3.17 (BIN1); also elsewhere on the board
LMIN2: U3.16 (BIN2); also elsewhere on the board
LMOUT+: MOTORL.1, U3.11 (BOUT1), U3.12 (BOUT1)
LMOUT-: MOTORL.6, U3.7 (BOUT2), U3.8 (BOUT2)
PWML: U3.15 (PWMB); also elsewhere on the board
PWMR: U3.23 (PWMA); also elsewhere on the board
RMIN1: U3.21 (AIN1); also elsewhere on the board
RMIN2: U3.22 (AIN2); also elsewhere on the board
RMOUT+: MOTORR.1, U3.1 (AOUT1), U3.2 (AOUT1)
RMOUT-: MOTORR.6, U3.5 (AOUT2), U3.6 (AOUT2)
STBY: R16.1, U3.19 (STBY)
VMOTOR: C11.1, Q2.2 (S), U3.13 (VM), U3.14 (VM), U3.24 (VM)


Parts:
C18, C19, C20, C21, C22, C23, C24: 1.0uF; 0603
C26: 0.1uF; 0603
JD0, JD1, JD2, JD3, JD4, JD5, JD6: QWIIC_Vertical; JST04_1MM_VERT
R28, R29, R30, R31, R32, R33, R34, R35, R36, R37, R38, R39, R40, R41: 4.7k; 0603
R49: 10k; 0603
R50: 1k; 0603
TEENSY_POWER: RED; LED-0603
U5: PCA9548A; TSSOP28
U$8, U$30, U$31, U$32, U$33, U$34, U$35, U$36, U$37, U$43, U$45, U$46, U$47, U$48: MOUNTINGHOLE2.5; MOUNTINGHOLE_2.5_PLATED

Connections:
3.3V: C18.1, C19.1, C20.1, C21.1, C22.1, C23.1, C24.1, C26.1, JD0.2, JD1.2, JD2.2, JD3.2, JD4.2, JD5.2, JD6.2, R28.1, R29.1, R30.1, R31.1, R32.1, R33.1, R34.1, R35.1, R36.1, R37.1, R38.1, R39.1, R40.1, R41.1, R49.2, TEENSY_POWER.A, U5.24 (VCC); also elsewhere on the board
GND: C18.2, C19.2, C20.2, C21.2, C22.2, C23.2, C24.2, C26.2, JD0.1, JD1.1, JD2.1, JD3.1, JD4.1, JD5.1, JD6.1, R50.1, U5.1 (A0), U5.2 (A1), U5.12 (GND), U5.21 (A2); also elsewhere on the board
I2CMUX_!RST: R49.1, U5.3 (!RST); also elsewhere on the board
unnamed: R50.2, TEENSY_POWER.C
SCL0: JD0.4, R29.2, U5.5 (SC0)
SCL1: JD1.4, R31.2, U5.7 (SC1)
SCL2: JD2.4, R33.2, U5.9 (SC2)
SCL3: JD3.4, R35.2, U5.11 (SC3)
SCL4: JD4.4, R37.2, U5.14 (SC4)
SCL5: JD5.4, R39.2, U5.16 (SC5)
SCL6: JD6.4, R41.2, U5.18 (SC6)
SCL_MAIN: U5.22 (SCL); also elsewhere on the board
SDA0: JD0.3, R28.2, U5.4 (SD0)
SDA1: JD1.3, R30.2, U5.6 (SD1)
SDA2: JD2.3, R32.2, U5.8 (SD2)
SDA3: JD3.3, R34.2, U5.10 (SD3)
SDA4: JD4.3, R36.2, U5.13 (SD4)
SDA5: JD5.3, R38.2, U5.15 (SD5)
SDA6: JD6.3, R40.2, U5.17 (SD6)
SDA_MAIN: U5.23 (SDA); also elsewhere on the board

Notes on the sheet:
Qwiic Connectors
Main
I2C Multiplex
Clear jumper JP4 to remove I2C pullup resistors


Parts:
C1, C2: 22pF; 0603-NO
C4: 0.1uF; 0603-NO
D1: 1n4148; SOD-323
R3: 10K; RESPACK_4X0603
R4: 10K; 0603-NO
U$6: BNO055
X2: 32.768; XTAL3215

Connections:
3.3V: R4.1, U$6.3 (VDD), U$6.4 (NBOOT_LOAD_PIN), U$6.8 (PIN8(SWCLK)), U$6.28 (VDDIO); also elsewhere on the board
GND: C1.1, C2.1, C4.1, R3.5 (2), R3.6 (2), U$6.2 (GND), U$6.10 (PIN10(GND)), U$6.15 (PIN15(GND)), U$6.16 (PIN16(GND)), U$6.17 (COM3/I2C_ADDR), U$6.18 (COM2(GND)), U$6.25 (GND); also elsewhere on the board
IMU_NRESET_3V: D1.A, R4.2, U$6.11 (NRESET)
IMU_RESET: D1.C; also elsewhere on the board
INT_3V: U$6.14 (INT)
unnamed: C1.2, U$6.27 (XIN32), X2.P$2
unnamed: C2.2, U$6.26 (XOUT32), X2.P$1
unnamed: C4.2, U$6.9 (CAP)
PS0_3V: R3.3 (1), U$6.6 (PS0)
PS1_3V: R3.4 (1), U$6.5 (PS1)
SCL_MAIN: U$6.19 (COM1/SCL/RX); also elsewhere on the board
SDA_MAIN: U$6.20 (COM0/SDA/TX); also elsewhere on the board

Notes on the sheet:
BNO055 IMU



Board: 2 copper layers, 95.0 x 77.5 mm, 115 parts (43 on the bottom side), 71 nets.

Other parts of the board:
U$7, U$23, U$28, U$29: MOUNTINGHOLE_2.5_PLATED_THICK

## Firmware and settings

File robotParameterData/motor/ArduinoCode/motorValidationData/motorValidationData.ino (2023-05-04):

// Determine the Motor Characteristics for GRITSBOTX 

// PIN DEFINITIONS 

// Motor A(left) and B(right) are connected to AIN1,AIN2 and BIN1 and BIN2 on the motor controller 

#include <Encoder.h>

//////DEFINE ENCODER OBJECTS FOR LEFT AND RIGHT WHEEL //////////////
Encoder motorLeft(5, 6);
Encoder motorRight(21,20);

//  Pin Definitions 
int STBY = 4; // motor driver enable 
int led = 13; // Teensy LED Pin 

// Motor A 
int PWMA = 9; // control the speed 
int AIN1 = 0; // direction 
int AIN2 = 1; // direction 

//Motor B 
int PWMB = 10; // speed control 
int BIN1 = 2; // direction 
int BIN2 = 3; // direction 


//Constants

float pi = 3.14159265359;

//Encoder Count Storage
int countR = 0; // Current count for RIGHT encoder.
int countL = 0; // Current count for LEFT encoder.

int oldCountR = 0;
int oldCountL = 0;

//Other Variables
float timeStart=0;
float timeStartStep=0;

float experimentTime = 60; //60 seconds.
float stepExperimentTime = 2000; // 2 Seconds in ms.

float samplingTime = 5; //10 ms sampling time.

//PID Stuff
float PIDMotorsTimeStart = 0;
float oldErrorL = 0;
float oldErrorR = 0;
float oldMotorPIDEncoderCountL = 0;
float oldMotorPIDEncoderCountR = 0;
float encoderCountsPerRotation = 12;
float motorGearRatio = 150.58;
float kpMotor = 6.01;
float kiMotor = 613;
float kdMotor = 0;
int motorL = 0;
int motorR = 0;

float desVel[5] = {random(-8,8), random(-8,8), random(-8,8), random(-8,8), random(-8,8)};//rad/s

int input = 0;

////////////////////// SETUP //////////////////////////////////
void setup() {
  // define the pins as outputs
  pinMode(STBY,OUTPUT);
  pinMode(led,OUTPUT);
  
  pinMode(PWMA,OUTPUT);
  pinMode(AIN1,OUTPUT);
  pinMode(AIN2,OUTPUT);

  pinMode(PWMB,OUTPUT);
  pinMode(BIN1,OUTPUT);
  pinMode(BIN2,OUTPUT);

  digitalWrite(led, LOW);    // turn the LED off by making the voltage LOW
  delay(1000);               // wait for a second

  Serial.begin(115200);

  while (!Serial) {
    ; // wait for serial port to connect. Needed for native USB
  }
  delay(1000);//Allow Time for Matlab to start.
  PIDMotorsTimeStart = millis();
}

//////////////// MAIN LOOP ////////////////////////////////////

void loop()                     
{ 
  for (int i = 0; i<5; i++){
    if (i == 0){
      timeStart = millis();
    }
    timeStartStep=millis();
    while (millis() - timeStartStep < stepExperimentTime){
      PIDMotorControl(desVel[i],desVel[i]);
      if (millis() - timeStart >= samplingTime){
        readEncoders();
        timeStart = millis();
        //Correct for wrap around
        if (countL < 0 && oldCountL > 0){
          countL = ((countL - (-2147483648)) + (2147483647 - oldCountL));
        }
        if (countR < 0 && oldCountR > 0){
          countR = ((countR - (-2147483648)) + (2147483647 - oldCountR)); // (rad)
        }
        oldCountR = countR;
        oldCountL = countL;
        Serial.print(int(countL));
        Serial.print(",");
        Serial.print(int(countR));
        Serial.print(",");
        Serial.print(int(millis()));
        Serial.print(",");
        Serial.println(desVel[i]);    
        Serial.flush();
       }
    }
  }
  

   stop();
   Serial.flush();
   Serial.print("Done");
   Serial.end();
   while(1){
      digitalWrite(led, HIGH);   // turn the LED on (HIGH is the voltage level)
      delay(1000);               // wait for a second
      digitalWrite(led, LOW);    // turn the LED off by making the voltage LOW
      delay(1000);               // wait for a second
   }
}
////////////////// FUNCTIONS //////////////////////////////////
void moveR(int motorSpeed){
  //Assume forward at first
  boolean in1 = HIGH;
  boolean in2 = LOW;

  //If motor speed is negative we want to rotate wheel backwards
  if (motorSpeed < 0){
     in1 = LOW;
     in2 = HIGH;
  }
   
  // Truncate PWM input to 255
  if (abs(motorSpeed)>255){
    motorSpeed = 255;
  }

  // Move the motor.
  digitalWrite(STBY, HIGH);
  digitalWrite(BIN1,in1);
  digitalWrite(BIN2,in2);
  analogWrite(PWMB, abs(motorSpeed)); 
}

void moveL(int motorSpeed){
  //Assume forward at first
  boolean in1 = LOW;
  boolean in2 = HIGH;

  //If motor speed is negative we want to rotate wheel backwards
  if (motorSpeed < 0){
     in1 = HIGH;
     in2 = LOW;
  }
   
  // Truncate PWM input to 255
  if (abs(motorSpeed)>255){
    motorSpeed = 255;
  }

  // Move the motor.
  digitalWrite(STBY, HIGH);
  digitalWrite(AIN1,in1);
  digitalWrite(AIN2,in2);
  analogWrite(PWMA, abs(motorSpeed));
}

void brake(){
  //Brakes the motors. (Locked to not rotate passively, this can be overcome by enough torque)
  digitalWrite(STBY, HIGH);
  
  analogWrite(PWMA, LOW);
  digitalWrite(AIN1, HIGH);
  digitalWrite(AIN2, HIGH);
  
  analogWrite(PWMB, LOW);
  digitalWrite(BIN1, HIGH);
  digitalWrite(BIN2, HIGH);
}

//Positive speed drives straight
void driveStraight(int motorSpeed){
  moveL(motorSpeed);
  moveR(motorSpeed);
}

//Positive speed turns right
void turn(int motorSpeed){
  moveL(motorSpeed);
  moveR(-motorSpeed);
}

void stop() {
  // Turns the motors off. (They can still rotate passively) 
  digitalWrite(STBY,LOW);
}

void readEncoders(){
  countR = -motorRight.read();
  countL = motorLeft.read();
}

void PIDMotorControl(float desLVel, float desRVel){
    /*Keeps the rotational speeds of the individual motors at setpoints desLVel and desRVel (rad/s).*/

    float timeStep = 10;

    if (millis() - PIDMotorsTimeStart >= timeStep){
      float PIDTimeStep = (millis() - PIDMotorsTimeStart)/1000;//Time step for controller to work on (s).

      readEncoders();

      // Error on individual motors for vel control
      float errorL = desLVel - 2 * pi * (countL - oldMotorPIDEncoderCountL) / (encoderCountsPerRotation * motorGearRatio * PIDTimeStep);
      float errorR = desRVel - 2 * pi * (countR - oldMotorPIDEncoderCountR) / (encoderCountsPerRotation * motorGearRatio * PIDTimeStep);
      float integralL = integralL + errorL * PIDTimeStep;
      float integralR = integralR + errorR * PIDTimeStep;
      float diffL = (oldErrorL - errorL) / PIDTimeStep;
      float diffR = (oldErrorR - errorR) / PIDTimeStep;
      oldErrorL = errorL;
      oldErrorR = errorR;
      oldMotorPIDEncoderCountL = countL;
      oldMotorPIDEncoderCountR = countR;

      motorL += int((kpMotor*errorL + kiMotor*integralL + kdMotor*diffL));
      motorR += int((kpMotor*errorR + kiMotor*integralR + kdMotor*diffR));

      moveL(motorL);
      moveR(motorR);
      
      PIDMotorsTimeStart = millis();
    }
}

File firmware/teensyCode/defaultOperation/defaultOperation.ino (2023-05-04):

#include <Adafruit_SPITFT_Macros.h>
#include <Adafruit_GFX.h>
#include <gfxfont.h>
#include <Adafruit_SPITFT.h>

#include <GritsbotX.h>

GritsbotX myRobot;
int garbage[2];

void setup() {
  Serial.begin(500000);
  myRobot.SETUP();
  myRobot.rainbow(10);
  myRobot.turnOffLED();
  myRobot.disableIR();
}

void loop() {
  // put your main code here, to run repeatedly:

  myRobot.getEncoderCounts(garbage);
  myRobot.checkCharging();
  if (myRobot.checkCharging()){ //If we're charging disable unnecessary current draws.
    myRobot.disableIR();
    //myRobot.turnOffLED();
  }
  myRobot.checkBattVoltage();

  myRobot.jsonSerialRead();
  myRobot.communicationCheck(500);
  myRobot.followCommands();  
}

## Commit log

2023-05-08 GRITSBot 3.0 Schematic and PCB
    [mainBoard_GRITSBot3-0_v14.sch, mainBoard_GRITSBot3-0_v22.brd]
2023-05-08 GRITSBot 3.0 circuit schematic pdf

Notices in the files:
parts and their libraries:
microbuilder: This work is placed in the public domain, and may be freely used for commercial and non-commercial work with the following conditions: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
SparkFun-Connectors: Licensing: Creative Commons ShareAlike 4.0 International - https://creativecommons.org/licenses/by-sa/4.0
